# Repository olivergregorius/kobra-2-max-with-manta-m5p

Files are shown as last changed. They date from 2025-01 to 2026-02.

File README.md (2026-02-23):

# Anycubic Kobra 2 Max with BigTreeTech Manta M5P

## Prologue

I recently purchased a Kobra 2 Max 3D printer from Anycubic. Especially the big build volume led to my decision buying this printer. I was aware that it has
just some closed-up version of Klipper installed, but as I was not that familiar with 3D printing that time, I paid far too little attention to what this could
mean to me and my prints.

### Issues arise

I was happy with my prints, especially those using PLA as filament. But when choosing ABS or ASA I experienced a little issue that bothered me: Regardless of
the settings in my slicer - I'm using PrusaSlicer - after the first layer was completed, the part cooling fan turned on to 100 %, leading the bed (set to 90 °C)
to cool down a bit. This caused an error after it had reached 85 °C, aborting the print immediately. I did some analysis, tried some different workarounds like
e.g. adding a `M107` or a `M106 S0` right after the first layer in the G-Code or before the second layer, but the only thing that worked... was... going to the
printer, waiting for the first layer to complete and turning off the fan by hand using the printer's control board.

### Looking for a solution

I was not happy with that. So I started looking for another solution. Vanilla Klipper seemed to be the "holy grail" for my issue. I read some reports about
installing Klipper on a Kobra 2. But as mentioned there, unfortunately this was **not** possible for a Kobra 2 Pro/Plus/Max with the built-in "TriGorilla_Spe_A"
mainboard. Long story short... since a 3D printer is just a framework with some stepper motors, moving all axes and the filament, and some heaters, this all can
be controlled by **any** mainboard designed for that. Thus, I chose to replace this board with another one, giving me the ability to install vanilla Klipper on,
to have full flexibility controlling my printer.

## Solution found - Presenting it to you so you can benefit

I just came across the website from [@1coderookie](https://github.com/1coderookie): [Kobra2MaxInsights](https://1coderookie.github.io/Kobra2MaxInsights/) which
basically describes every little part of the printer - it is just a gold mine for everyone who aims for modding this printer. BTW, there are corresponding URLs
for the Kobra 2 Pro and Plus, too. But all in all the printers of the Kobra 2 Pro/Plus/Max series do not differ that much at all (except for the printing
volume, of course).

1coderookie there describes a mod, replacing the stock mainboard with a MKS Robin Nano v3.1. As I already had taken a lookaround and found the BigTreeTech Manta
boards very promising, I chose to go with a [Manta M5P](https://biqu.equipment/de/products/manta-m4p-m8p?variant=40215553900642). The only problem was that the
stock connectors were not compatible with the sockets on the M5P board. I did not want to modify the stock connectors, I just wanted an in-place replacement of
the board, so if anything does not work as planned I could simply switch back to the stock mainboard, having a fully functional printer again.

So I ordered a Manta M5P board along with a CB1 computing module, five TMC2209 steppers and a heatsink for the CB1. Furthermore, I ordered some PH, XH and PHB
wires of different sizes as described in 1coderookie's modding howto to build the required adapter wires. In the following I will describe my resulting setup
for you to use it either for a 1:1 adaption or as a starting point for further improvements.

### Wire mapping

**Stock mainboard pinout**



Source: https://github.com/codexnovus/reverse-engineering-the-kobra2-pro/blob/60daed37d88431c6e6d83d84898fbabf0f436f80/motherboard/motherboard-pinout.svg

**Manta M5P pinout**

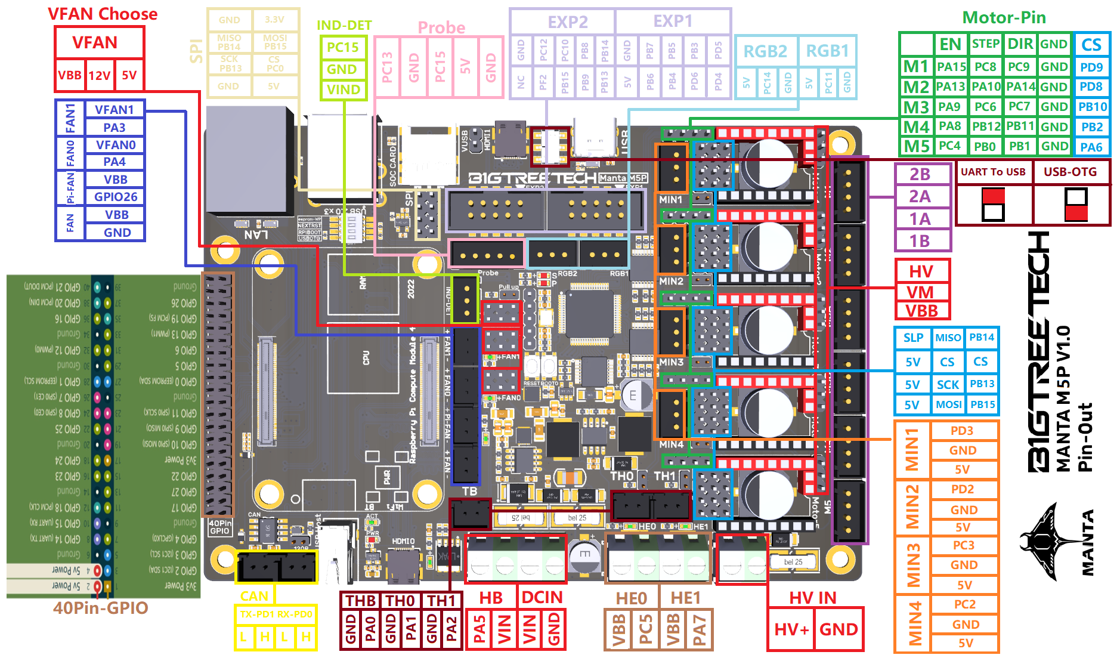
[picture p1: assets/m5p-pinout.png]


Source: https://github.com/bigtreetech/Manta-M5P/blob/e1692ada06ddcb63f567f5ddfb9bfab581a42240/Hardware/BIGTREETECH%20MANTA%20M5P%20V1.0-Pin.png

In the following table you find the mapping of the stock mainboard connector pins to the Manta M5P connector pins.

| Part | Stock Mainboard Connector | Pin | Manta M5P Connector | Pin  |
|:---|---|---|---|---|
| Power Supply | POWER | PSU+ | DCIN | VIN  |
| | POWER | PSU- | DCIN | GND  |
| Hotbed Power Supply | HOTBED | HOTBED+  | HB | VIN  |
| | HOTBED | HOTBED-  | HB | PA5  |
| Mainboard Fan | MB-FAN | FAN+ | FAN | VBB  |
| | MB-FAN | FAN- | FAN | GND  |
| Hotbed Thermistor | T1 | T1 | THB | PA0  |
| | T1 | GND | THB | GND  |
| Calibration Switch | CALIBRATION | S | MIN3 | PC3  |
| | CALIBRATION | GND | MIN3 | GND  |
| Hotbed Acceleration Sensor | ACC-SENSOR | GND | RGB1 | GND  |
| | ACC-SENSOR | MOSI | EXP2 | PB15 |
| | ACC-SENSOR | MISO | EXP2 | PB14 |
| | ACC-SENSOR | SCLK | EXP2 | PB13 |
| | ACC-SENSOR | CS | EXP1 | PB4  |
| | ACC-SENSOR | GND | RGB1 | GND  |
| | ACC-SENSOR | 5V | RGB1 | 5V |
| Y-Axis Motor | Y-CON | A1 | M2 | 1A |
| | Y-CON | A2 | M2 | 1B |
| | Y-CON | B1 | M2 | 2A |
| | Y-CON | B2 | M2 | 2B |
| Y-Axis Limit Switch | Y-CON | GND | MIN2 | GND  |
| | Y-CON | LIMIT | MIN2 | PD2  |
| Printhead Hotend Power Supply | E-CON | H+ | HE0 | VBB  |
| | E-CON | H- | HE0 | PC5  |
| Printhead Acceleration Sensor | E-CON | MOSI | EXP2 | PB15 |
| | E-CON | MISO | EXP2 | PB14 |
| | E-CON | SCLK | EXP2 | PB13 |
| | E-CON | CS | EXP1 | PB5  |
| Printhead Inductive Level Sensor | E-CON | LEVEL | EXP2 | PC12 |
| Printhead Hotend Thermistor | E-CON | T0 | TH0 | PA1  |
| Printhead GND | E-CON | GND | RGB2 | GND  |
| Printhead 5V Supply | E-CON | 5V | RGB2 | 5V |
| Printhead 24V Supply | E-CON | 24V | IND-DET | VIND |
| Printhead Heatsink Cooling Fan | E-CON | F1 | FAN1 | PA3  |
| Printhead Part Cooling Fan | E-CON | F0 | FAN0 | PA4  |
| Extruder Motor | E-CON | A1 | M4 | 1A |
| | E-CON | A2 | M4 | 1B |
| | E-CON | B1 | M4 | 2A |
| | E-CON | B2 | M4 | 2B |
| Z-Axis Motor Left | ZL | A1 | M3A | 1A |
| | ZL | A2 | M3A | 1B |
| | ZL | B1 | M3A | 2A |
| | ZL | B2 | M3A | 2B |
| Z-Axis Motor Right | ZR | A1 | M3B | 1A |
| | ZR | A2 | M3B | 1B |
| | ZR | B1 | M3B | 2A |
| | ZR | B2 | M3B | 2B |
| X-Axis Limit Switch | X-CON | X LIMIT  | MIN1 | PD3  |
| | X-CON | GND | MIN1 | GND  |
| Filament Runout Sensor | X-CON | GND | MIN4 | GND  |
| | X-CON | FILAMENT | MIN4 | PC2  |
| X-Axis Motor | X-CON | A1 | M1 | 1A |
| | X-CON | A2 | M1 | 1B |
| | X-CON | B1 | M1 | 2A |
| | X-CON | B2 | M1 | 2B |

### printer.cfg

You can find a basic printer.cfg [here](config/printer.cfg).

### Mainboard enclosure

You can find the parts of the mainboard enclosure [here](assets/prints). With the provided STL or 3MF files you can print the enclosure on your own.

### What does not work?

Unfortunately, I was not able to get the printhead's accelerometer working. I don't really have an idea what the problem might be, but I found out that it seems
to have something to do with the wiring of the printhead's inductive sensor (probe). If I disconnected the probe (PC12) the accelerometer could be queried using
the `ACCELEROMETER_QUERY` macro. If I connected it again, the console showed an error `Invalid lis2dw id got 8 vs 44`. The hotbed accelerometer worked without
any issues.

I decided to remove the corresponding configuration parts from the [printer.cfg](config/printer.cfg). I ordered an ADXL345 v2.0 from Bigtreetech that I just
connect via USB and do the resonance measurement for each axis after another. Since the resonance measurement is only required to be done if the overall printer
setup changes, this is a feasible solution for me.

# Disclaimer

By using the content in this repository, you acknowledge that you do so at your own risk. I am not liable for any damages or issues that may arise from
attempting the modifications or any other use of this material. The firmware mentioned is proprietary and not included here. For takedown requests or
suggestions, please contact me directly.

I am not affiliated with, or sponsored by any of the companies or persons mentioned in this repository. All product and company names are the registered
trademarks of their original owners. The use of any trade name or trademark is for identification and reference purposes only and does not imply any association
with the trademark holder of their product brand.

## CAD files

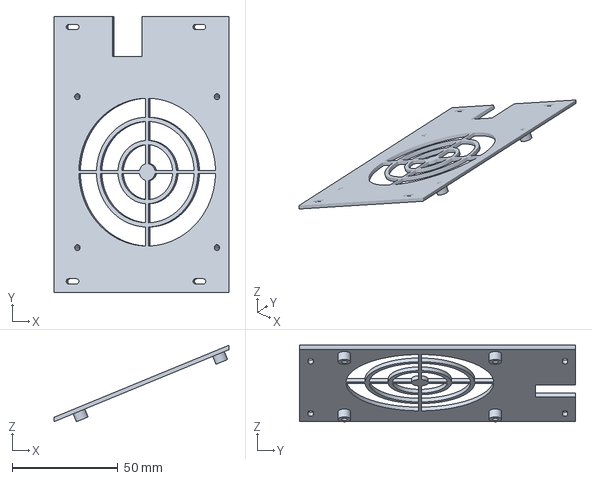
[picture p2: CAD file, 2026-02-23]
assets/prints/m5p-fan.3mf
82.9 x 130.8 x 36.3 mm

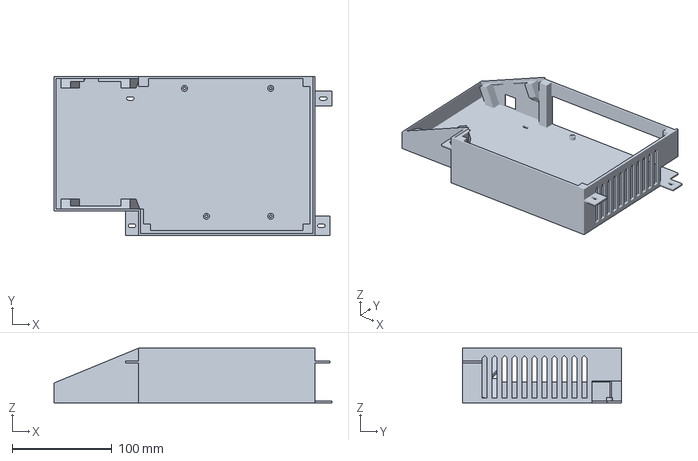
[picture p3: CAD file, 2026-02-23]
assets/prints/m5p-box.3mf
279.0 x 160.0 x 55.0 mm

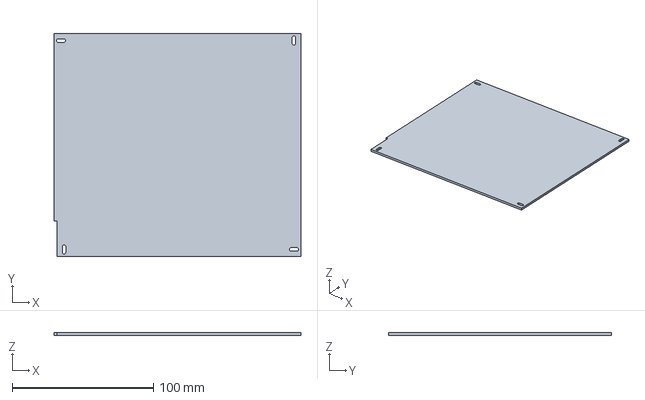
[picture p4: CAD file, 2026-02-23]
assets/prints/m5p-lid.3mf
174.9 x 157.9 x 2.00 mm

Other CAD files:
assets/prints/m5p-box.stl
assets/prints/m5p-fan.stl
assets/prints/m5p-lid.stl

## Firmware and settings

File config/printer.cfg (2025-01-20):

# This file contains common pin mappings for the BIGTREETECH Manta M5P
# To use this config, the firmware should be compiled for the
# STM32G0B1 with a "8KiB bootloader" "8 MHz crystal"
# and "USB (on PA11/PA12)" or "CAN bus (on PD0/PD1)".

# Configuration for Anycubic Kobra 2 Max with BIGTREETECH Manta M5P

[include mainsail.cfg]

[mcu]
serial: /dev/serial/by-id/usb-Klipper_stm32g0b1xx_<your mcu id>-if00
restart_method: command

[gcode_arcs]

[pause_resume]

[exclude_object]

[printer]
kinematics: cartesian
max_velocity: 300
max_accel: 2000
max_z_velocity: 16
max_z_accel: 500
square_corner_velocity: 15

# KobraOS stock settings for Kobra 2 Max, just as a reference
# kinematics: cartesian
# max_velocity: 500.000000
# max_accel: 10000.000000
# max_z_velocity: 16.000000
# max_z_accel: 3000.000000
# minimum_z_position: -20.000000
# square_corner_velocity: 15.000000

#
# X-Axis
#
[stepper_x]
step_pin: PC8
dir_pin: !PC9
enable_pin: !PA15
microsteps: 16
rotation_distance: 40
endstop_pin: !PD3
position_endstop: -8
position_max: 420
position_min: -10
homing_speed: 50
second_homing_speed: 10
homing_retract_dist: 5

[tmc2209 stepper_x]
uart_pin: PD9
run_current: 1.4
hold_current: 0.7
sense_resistor: 0.075
stealthchop_threshold: 0

#
# Y-Axis
#
[stepper_y]
step_pin: PA10
dir_pin: PA14
enable_pin: !PA13
microsteps: 16
rotation_distance: 40
endstop_pin: !PD2
position_endstop: -12
# Needs to be +20 related to the border of the printbed to be able to do Z-homing using the Z endstop switch
position_max: 440
position_min: -15
homing_speed: 50
second_homing_speed: 10
homing_retract_dist: 5

[tmc2209 stepper_y]
uart_pin: PD8
run_current: 1.9
hold_current: 1.0
sense_resistor: 0.075
stealthchop_threshold: 0

#
# Z-Axis
#
[stepper_z]
step_pin: PC6
dir_pin: !PC7
enable_pin: !PA9
microsteps: 16
rotation_distance: 8
endstop_pin: PC3
# Setting the position_endstop to -5 to avoid crashing the nozzle into the printing bed before the Z endstop calibration was done
#position_endstop: -5
position_max: 500
position_min: -5
homing_speed: 10
second_homing_speed: 5
homing_retract_dist: 5

[tmc2209 stepper_z]
uart_pin: PB10
run_current: 1.8
hold_current: 1.0
sense_resistor: 0.075
stealthchop_threshold: 999999

[safe_z_home]
# Nozzle position of Z endstop switch
home_xy_position: 389.5, 436.5
speed: 200
z_hop: 15
z_hop_speed: 8.0

#
# Extruder
#
[extruder]
step_pin: PB12
dir_pin: !PB11
enable_pin: !PA8
microsteps: 16
# May need adjustment for your setup, see the official Klipper docs: https://www.klipper3d.org/Rotation_Distance.html#calibrating-rotation_distance-on-extruders
rotation_distance: 6.684
nozzle_diameter: 0.400
filament_diameter: 1.750
heater_pin: PC5
sensor_type: EPCOS 100K B57560G104F
sensor_pin: PA1
#control: pid
#pid_kp: 20.611
#pid_ki: 0.875
#pid_kd: 121.347
min_temp: 0
max_temp: 260
# Default pressure advance for PLA, may need adjustment for your setup
pressure_advance: 0.05

[tmc2209 extruder]
uart_pin: PB2
run_current: 0.8
hold_current: 0.4
sense_resistor: 0.075
stealthchop_threshold: 999999

#
# Printing Bed
#
[heater_bed]
heater_pin: PA5
sensor_type: ATC Semitec 104GT-2
sensor_pin: PA0
#control: pid
#pid_kp: 74.066
#pid_ki: 0.872
#pid_kd: 1572.040
min_temp: 0
max_temp: 90

#
# Fans
#
# Part cooling fan
[fan]
pin: PA4

# Heatsink cooling fan of the hotend
[heater_fan hotend_cooling_fan]
pin: PA3

#
# Filament runout switch
#
[filament_switch_sensor filament_sensor]
switch_pin: !PC2
runout_gcode: PAUSE
insert_gcode: RESUME

#
# Probe
#
[probe]
pin: PC12
x_offset: 24.0
y_offset: 13.4
# Not relevant if homing is done via Z endstop switch
z_offset: 0.0
speed: 4
lift_speed: 8
samples: 5
sample_retract_dist: 5
samples_result: average
samples_tolerance: 0.05
samples_tolerance_retries: 5

[bed_mesh]
# All coordinates are relative to the probe!
speed: 60.0
horizontal_move_z: 5.0
mesh_min: 40, 40
mesh_max: 380, 380
probe_count: 7, 7
mesh_pps: 3, 3
algorithm: bicubic
# Center of the bed
zero_reference_position: 210, 210

#
# Misc
#
[board_pins]
aliases:
    # EXP1 header
    EXP1_1=PD5, EXP1_3=PB3, EXP1_5=PB5, EXP1_7=PB7, EXP1_9=<GND>,
    EXP1_2=PD4,  EXP1_4=PD6, EXP1_6=PB4, EXP1_8=PB6, EXP1_10=<5V>,
    # EXP2 header
    EXP2_1=PB14, EXP2_3=PB8, EXP2_5=PC10, EXP2_7=PC12,  EXP2_9=<GND>,
    EXP2_2=PB13, EXP2_4=PB9, EXP2_6=PB15, EXP2_8=<RST>, EXP2_10=<NC>

#*# <---------------------- SAVE_CONFIG ---------------------->
#*# DO NOT EDIT THIS BLOCK OR BELOW. The contents are auto-generated.
#*#
#*# [extruder]
#*# control = pid
#*# pid_kp = 20.611
#*# pid_ki = 0.875
#*# pid_kd = 121.347
#*#
#*# [heater_bed]
#*# control = pid
#*# pid_kp = 74.066
#*# pid_ki = 0.872
#*# pid_kd = 1572.040
#*#
#*# [stepper_z]
#*# position_endstop = -5.000

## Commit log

2025-01-20 Extended README.md, added required files
    [printer.cfg]
2026-02-23 Added M5P enclosure model files
    [m5p-box.3mf, m5p-box.stl, m5p-fan.3mf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]
